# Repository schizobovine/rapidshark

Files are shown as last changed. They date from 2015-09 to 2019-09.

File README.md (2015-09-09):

# RapidShark
Nerf RapidStrike CS-18 mod using an Arduino and LiPo battery upgrade to rain
foamy annoyance upon one's enemies.

The name originally came from my initial idea to use a pair of NSR Shark 40krpm
motors, originally for 12V slot car racing. It quickly became a reference to
Randall Munroe's [XKCD comic about lowering one's standards for success as a
project wears on...]<https://xkcd.com/349/>

# Versions

This project has undergone a number of major and minor redesigns, and my
documentation isn't exactly the best, especially for earlier versions where I
assumed this would be a quick hack involving relatively little electronics
knowledge (oh, to be 3 years younger and less naive...).

* Mark I
*  Completed build
*  Used slightly larger motors: 24mm 12V 12850rpm [PAN14EE12AA1]<http://www.digikey.com/product-detail/en/PAN14EE12AA1/P14346-ND/2417070>
*  Covered cut-outs for above with some horribly done epoxy work
*  4S LiPo battery (14.8V nominal)
*  Flywheels ran directly off battery voltage
*  Rate of fire controlled via diodes (1N5209's?) in series
*  Segmented LED display only showed battery voltage.
*  Extremely noisy, had jamming issues especially at higher ROF
*  Very clumsy controls (giant knob on the side for ROF)
*  Overall, kinda crappy prototype

* Mark II
*  Never finished build
*  Originally going to be 2S LiPo based
*  Proved too noisy for reasonable use

* Mark III
*  Completed build
*  Same [PAN14EE12AA1]<http://www.digikey.com/product-detail/en/PAN14EE12AA1/P14346-ND/2417070> as in Mark I
*  Used heat gun to deform plastic to accomodate motors
*  4S LiPo battery (14.8V nominal)
*  Flywheels again directly off line voltage
*  Rate of fire controlled via stupidly big linear regulator (LM335, then LT1083)
*  Custom PCB from OSHPark for speed controller
*  Actually bothered to paint this one
*  Slightly better slide switch for ROF control
*  Added pushbutton laser "sight" because reasons
*  First attempt at ammo counter using SparkFun Pro Mini 5V to drive a 2 digit segmented display
*  Detected shots at first using IR LED & photodiode, but was too noisy so went to reed switch
*  Button panel for fiddling with/resetting counter
*  Counter was awesome but proved very unreliable in practice
*  Noticable voltage drop-out during flywheel spin-up

* Mark IV
*  Work in progess
*  Skipping paint job to make this one a "sleeper" model
*  Motors unselected but will be 130 Mabuchi form-factor to fit in existing case with little modification
*  Will feature two proper H-bridges, the [Pololu VNH5019 Motor Driver Carrier]<https://www.pololu.com/product/1451>
*  Since the H-bridges will be electronically controlled, switched to subminiature microswitches hooked up to uC (instead of giant 15A microswitches directly flipping current around)
*  [Adafruit Metro Mini]<https://www.adafruit.com/products/2590> as main controller
*  OLED display (either SparkFun Microview or Ye Olde Generic From Ebay)
*  IR interrupter for dart firing detection confirmation, in combination with mechanical position detection for the dart pusher.
*  Whole slew of small custom PCB's to aid in wiring

# License

* AVR C code (basically, everything under the firmware directory) is licensed under the GPLv2.0.
* Everything else is Creative Commons 4.0, Attribution-Share-Sharealike (CC-4.0-BY-SA)

# Acknowledgements

I would not be nearly as far along (or in the ICU from exploding batteries) if
not for the help and previous work & knowledge of
[torukmakto4]<http://torukmakto4.blogspot.co.uk/>; read some of the linked
posts below for a good breakdown of the basic fire control circuit in the
RapidStrike.

I also would like to thank the folks from Blastersmiths UK for their
information shared on [Diaries of a Nerf
Armorurer]<http://nerfarmourer.tumblr.com>, as it both provided inspiration,
guidance, and a lot of helpful pictures for this project.

# References

[The Dart Zone: Wiring and electrical practices]<http://torukmakto4.blogspot.co.uk/2013/04/tech-wiring-and-electrical-practices.html>
[The Dart Zone: Standard Rapidstrike, an Illustrated Guide]<http://torukmakto4.blogspot.co.uk/2013/10/standard-rapidstrike-illustrated-guide.html>
[The Dart Zone: Why compensating for resistance using additional voltage is bad design]<http://torukmakto4.blogspot.co.uk/2014/05/why-compensating-for-resistance-using.html>
[Diaries of a Nerf Armourer: 'Sharked' Rapidstrike CS-18 - Raja and Triakis]<http://nerfarmourer.tumblr.com/post/59029888581/sharked-rapidstrike-cs-18-raja-and-triakis>
[Diaries of a Nerf Armourer: NSR Shark 40 Necrospy]<http://nerfarmourer.tumblr.com/post/69776618533/nsr-shark-40-necrospy>
[Diaries of a Nerf Armourer: Rapidstrike Modification Guide]<http://nerfarmourer.tumblr.com/post/57957334515/rapidstrike-modification-guide-also-commissions>

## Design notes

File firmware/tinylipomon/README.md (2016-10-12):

Tiny Lipo Battery Monitor
=====================

Small ATTiny84 board for monitoring high power lithium polymer batteries
connected in series. Due to differences in manufacturing, the cells in them
will often vary in voltage and capacity, so a close eye must be kept to make
sure none are close to over-charge (>4.2V/cell) or near drained (<3.2V/cell).

This is the firmware for the project, which you should be able to load on an
ATTiny84 of your own using the Ardunio IDE (1.6+) and the attiny board add-on
(available in the board manager).

Probably deserves it's own project, but for now getting stashed here.

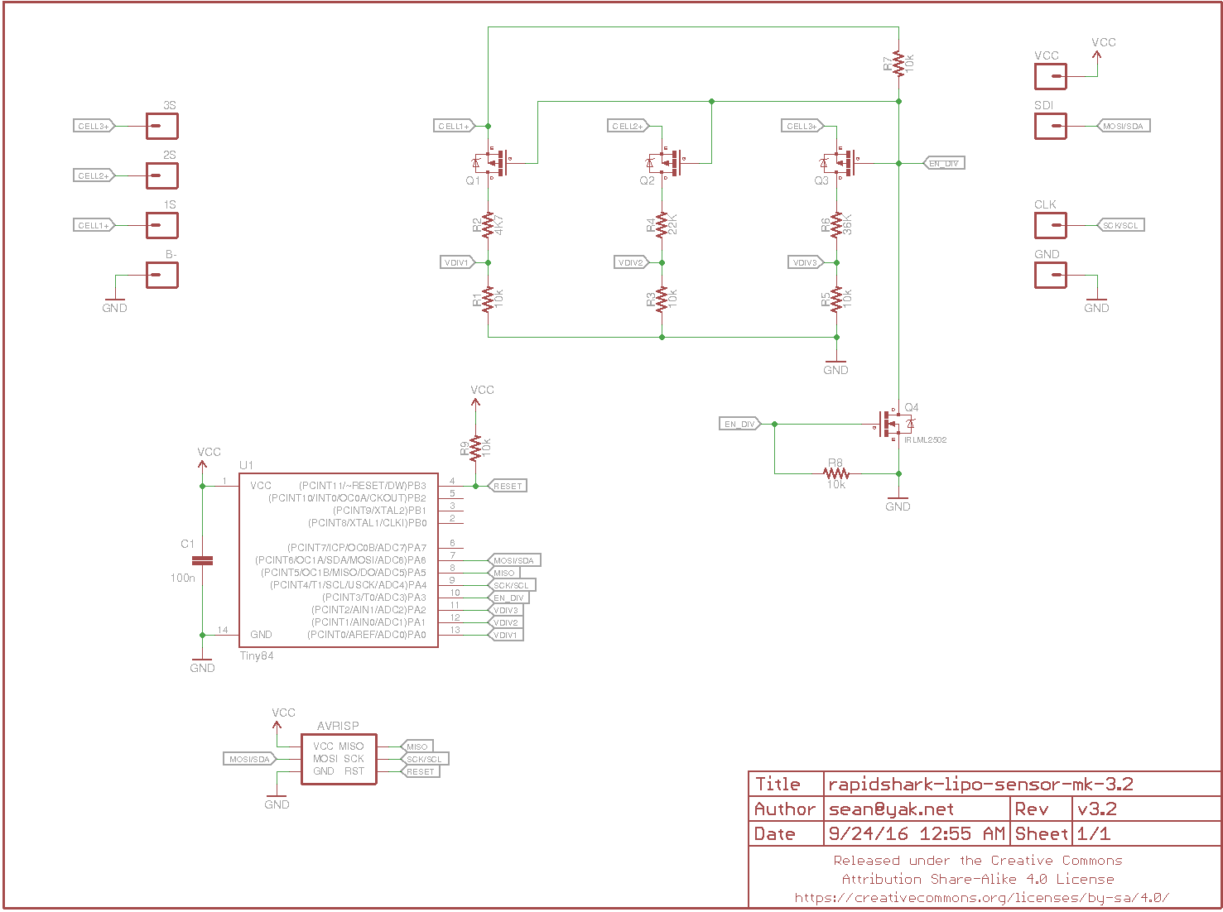
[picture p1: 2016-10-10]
hardware/rapidshark-lipo-sensor-mk-3.2.sch.png

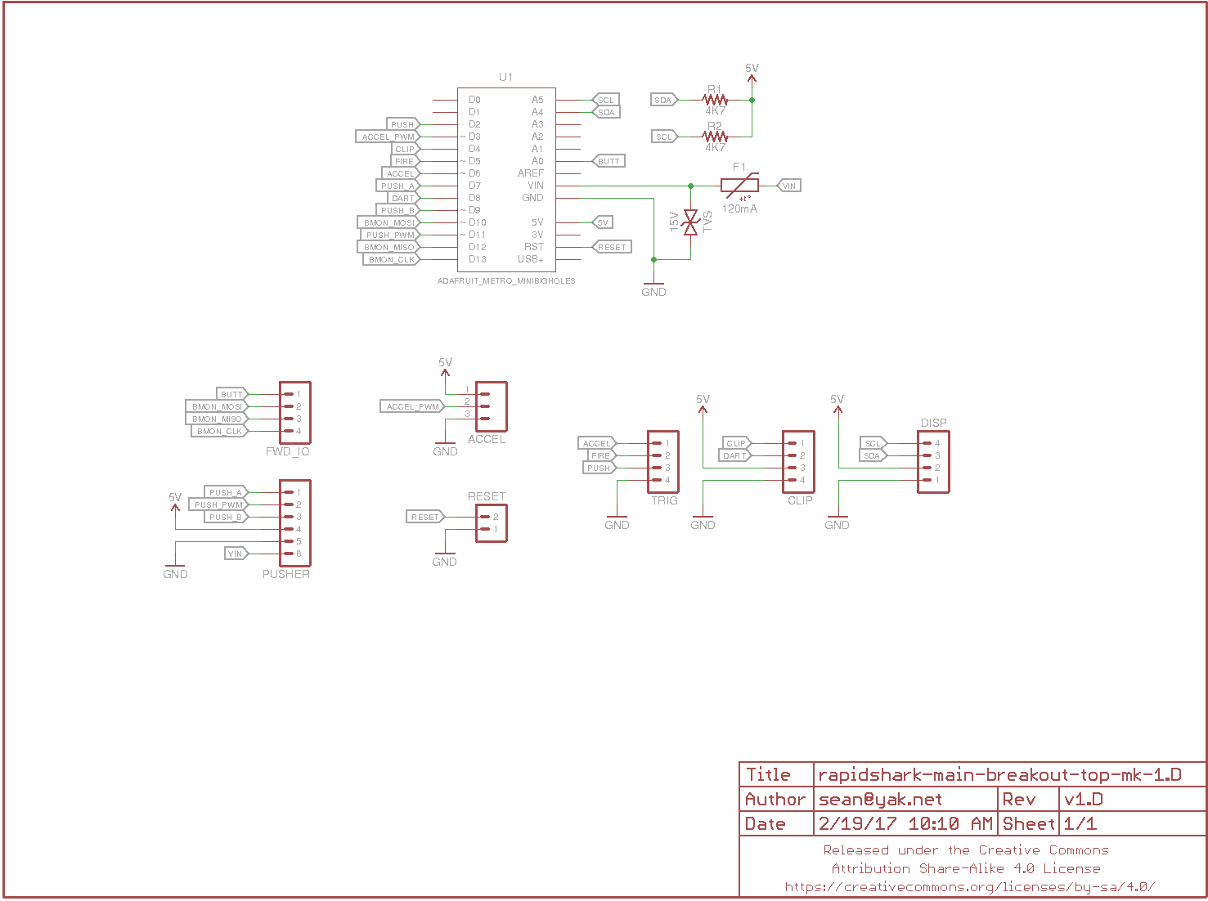
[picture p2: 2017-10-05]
hardware/rapidshark-main-breakout-top-mk-1.D.png

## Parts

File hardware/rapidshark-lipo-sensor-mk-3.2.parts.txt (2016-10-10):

Partlist

Exported from rapidshark-lipo-sensor-mk-3.2.sch at 10/8/16 1:10 AM

EAGLE Version 7.5.0 Copyright (c) 1988-2015 CadSoft

Assembly variant: 

Part     Value                        Device                         Package             Library  Sheet

1S       M01PTH-0.9MM                 M01PTH-0.9MM                   1X01-0.9MM          a_parts  1
2S       M01PTH-0.9MM                 M01PTH-0.9MM                   1X01-0.9MM          a_parts  1
3S       M01PTH-0.9MM                 M01PTH-0.9MM                   1X01-0.9MM          a_parts  1
AVRISP   AVR_SPI_PRG_6SMD_TEST_POINTS AVR_SPI_PRG_6SMD_TEST_POINTS   2X3_SMD_TEST_POINTS A_butts  1
B-       M01PTH-0.9MM                 M01PTH-0.9MM                   1X01-0.9MM          a_parts  1
C1       100n                         CAPACITOR-CERAMICC0603-TIGHTER C0603-TIGHTER       a_parts  1
CLK      M01PTH-0.9MM                 M01PTH-0.9MM                   1X01-0.9MM          a_parts  1
GND      M01PTH-0.9MM                 M01PTH-0.9MM                   1X01-0.9MM          a_parts  1
Q1                                    MOSFET-PCHANNELSOT-23          SOT23               a_parts  1
Q2                                    MOSFET-PCHANNELSOT-23          SOT23               a_parts  1
Q3                                    MOSFET-PCHANNELSOT-23          SOT23               a_parts  1
Q4       IRLML2502                    MOSFET-NCHANNELIRLML2502       SOT23               a_parts  1
R1       10k                          RESISTORR0603-TIGHTER          R0603-TIGHTER       a_parts  1
R2       4K7                          RESISTORR0603-TIGHTER          R0603-TIGHTER       a_parts  1
R3       10k                          RESISTORR0603-TIGHTER          R0603-TIGHTER       a_parts  1
R4       22K                          RESISTORR0603-TIGHTER          R0603-TIGHTER       a_parts  1
R5       10k                          RESISTORR0603-TIGHTER          R0603-TIGHTER       a_parts  1
R6       36K                          RESISTORR0603-TIGHTER          R0603-TIGHTER       a_parts  1
R7       10k                          RESISTORR0603-TIGHTER          R0603-TIGHTER       a_parts  1
R8       10k                          RESISTORR0603-TIGHTER          R0603-TIGHTER       a_parts  1
R9       10k                          RESISTORR0603-TIGHTER          R0603-TIGHTER       a_parts  1
SDI      M01PTH-0.9MM                 M01PTH-0.9MM                   1X01-0.9MM          a_parts  1
U1       Tiny84                       ATTINY84                       SO14                A_butts  1
VCC      M01PTH-0.9MM                 M01PTH-0.9MM                   1X01-0.9MM          a_parts  1

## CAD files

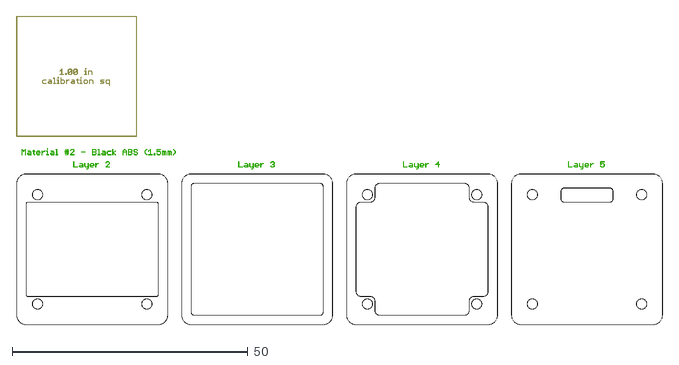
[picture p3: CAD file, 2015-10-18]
hardware/case-for-oled-mk-1.1-abs-black-1.5mm.dxf
137.1 x 65.5

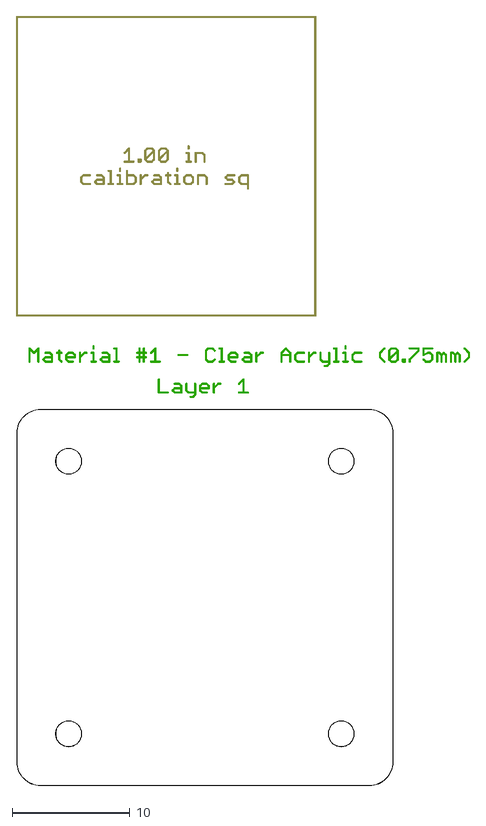
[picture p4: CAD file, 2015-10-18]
hardware/case-for-oled-mk-1.1-pmma-clear-0.75mm.dxf
38.6 x 65.5

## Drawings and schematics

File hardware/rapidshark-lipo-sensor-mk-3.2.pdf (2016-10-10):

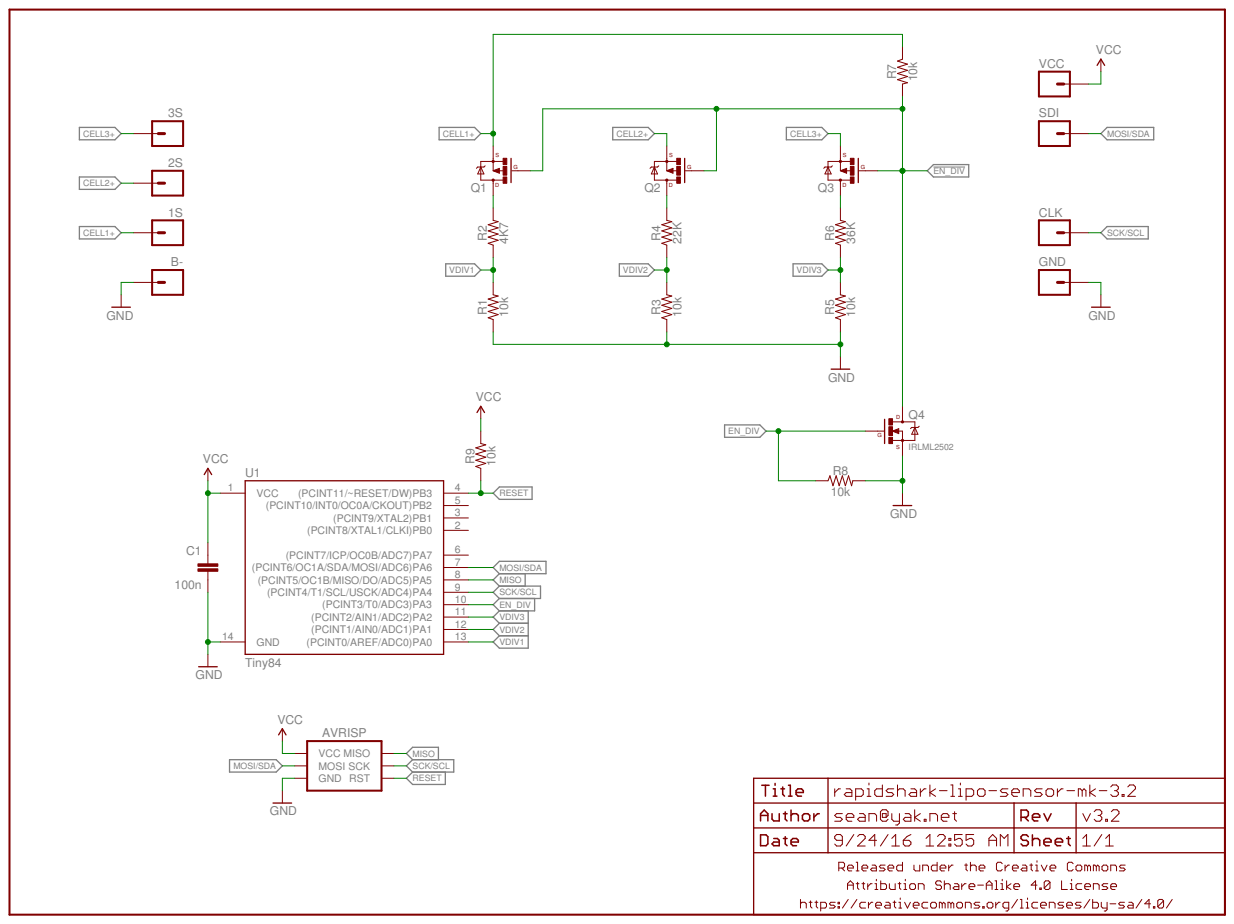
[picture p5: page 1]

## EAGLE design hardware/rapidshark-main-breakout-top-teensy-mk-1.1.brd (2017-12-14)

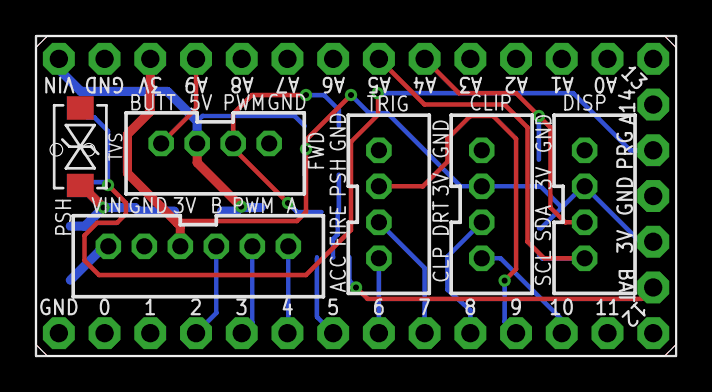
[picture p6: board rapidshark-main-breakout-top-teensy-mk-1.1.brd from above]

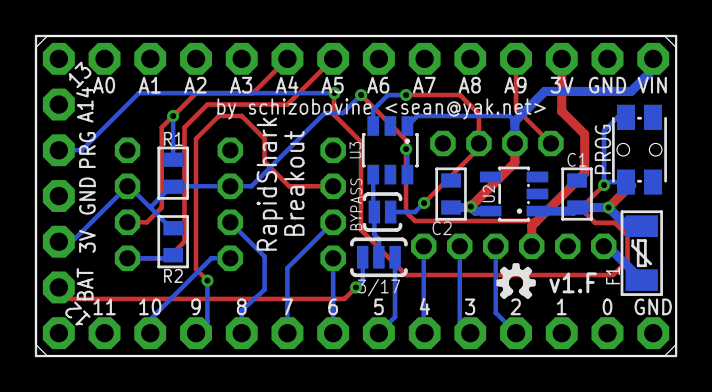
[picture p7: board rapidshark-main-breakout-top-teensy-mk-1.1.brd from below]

Board: 2 copper layers, 35.6 x 17.8 mm, 19 parts (12 on the bottom side), 21 nets.

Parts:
3/17: PAD-JUMPER-3-NO_YES_SILK_FULL_BOX_SMALLER
BYPASS: JUMPER-PAD-2-NOYES_SILK; PAD-JUMPER-2-NO_YES_SILK
C1: 1uF; C0603-TIGHTER
C2: 2.2uF; C0603-TIGHTER
CLIP: M04JST-PTH-VERT; JST-4-PH-VERT-PTH
DISP: M04JST-PTH-VERT; JST-4-PH-VERT-PTH
F1: 120mA; PTC-1206
FRAME1: FRAME-LETTERNO_PACKAGE; DUMMY
FWD: M04JST-PTH-VERT; JST-4-PH-VERT-PTH
PROG: SPST-NO-TACTCK-PTS840-GK; TACTILE-SMD-CK-PTS840-GK
PSH: M06JST-PH-PTH-VERT; JST-6-PH-VERT-PTH
R1, R2: 4K7; R0603-TIGHTER
TRIG: M04JST-PTH-VERT; JST-4-PH-VERT-PTH
TVS: 15V; SMA-DIODE-TVS-BIDIR
U1: TEENSY-3.1-OUTERPTH; TEENSY-3.1_OUTERONLY
U2: MIC5235; SOT23-5
U3: SN74LVC1T45SOT23-6; SOT23-6
U$3: OSHWLOGO_TINY_SILKONLY

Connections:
3.3V: CLIP.2, DISP.2, PSH.4, R1.2, R2.2, U1.3.3V, U1.3V, U3.6
5: 3/17.1, U1.5
5V: C2.1, FWD.3, U1.VIN, U2.5, U3.1
17: 3/17.3, U1.VBAT
ACCEL: TRIG.4, U1.6
ACCEL_PWM: 3/17.2, BYPASS.1, U3.4
ACCEL_PWM_5V: BYPASS.2, FWD.2, U3.3
BUTT: FWD.4, U1.23
CLIP: CLIP.4, U1.10
DART: CLIP.3, U1.8
FIRE: TRIG.3, U1.7
GND: C1.2, C2.2, CLIP.1, DISP.1, FWD.1, PROG.3, PROG.4, PSH.5, TRIG.1, TVS.1, U1.AGND, U1.GND, U1.GND1, U2.2, U3.2, U3.5
PROG: PROG.1, PROG.2, U1.PROG
PUSH: TRIG.2, U1.9
PUSH_A: PSH.1, U1.4
PUSH_B: PSH.3, U1.2
PUSH_PWM: PSH.2, U1.3
SCL: DISP.4, R2.1, U1.19
SDA: DISP.3, R1.1, U1.18
VIN: C1.1, F1.2, TVS.2, U2.1, U2.3
VRAW: F1.1, PSH.6

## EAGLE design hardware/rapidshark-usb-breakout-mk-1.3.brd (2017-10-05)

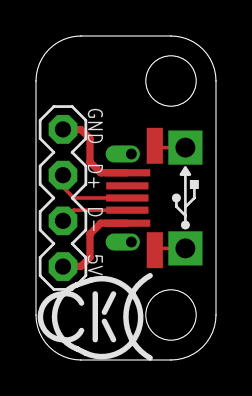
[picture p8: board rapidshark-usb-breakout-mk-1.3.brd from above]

Board: 2 copper layers, 10.0 x 18.0 mm, 4 parts (1 on the bottom side), 4 nets.

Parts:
FRAME1: FRAME-LETTERNO_PACKAGE; DUMMY
JP1: M04PTH-CENTERED; 1X04-PTH-VERT-CENTER
U$1: COW_SMALL_NOTEXT
USB1: USB-AB-SHIELDFCI-10103594-USB-MICRO-B-EVENLESS; FCI-10103594-USB-MICRO-B-EVENLESS

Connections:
5V: JP1.4, USB1.1
DATA_M: JP1.3, USB1.2
DATA_P: JP1.2, USB1.3
GND: JP1.1, USB1.5, USB1.SHIELD@1, USB1.SHIELD@2, USB1.SHIELD@3, USB1.SHIELD@4, USB1.SHIELD@5, USB1.SHIELD@6

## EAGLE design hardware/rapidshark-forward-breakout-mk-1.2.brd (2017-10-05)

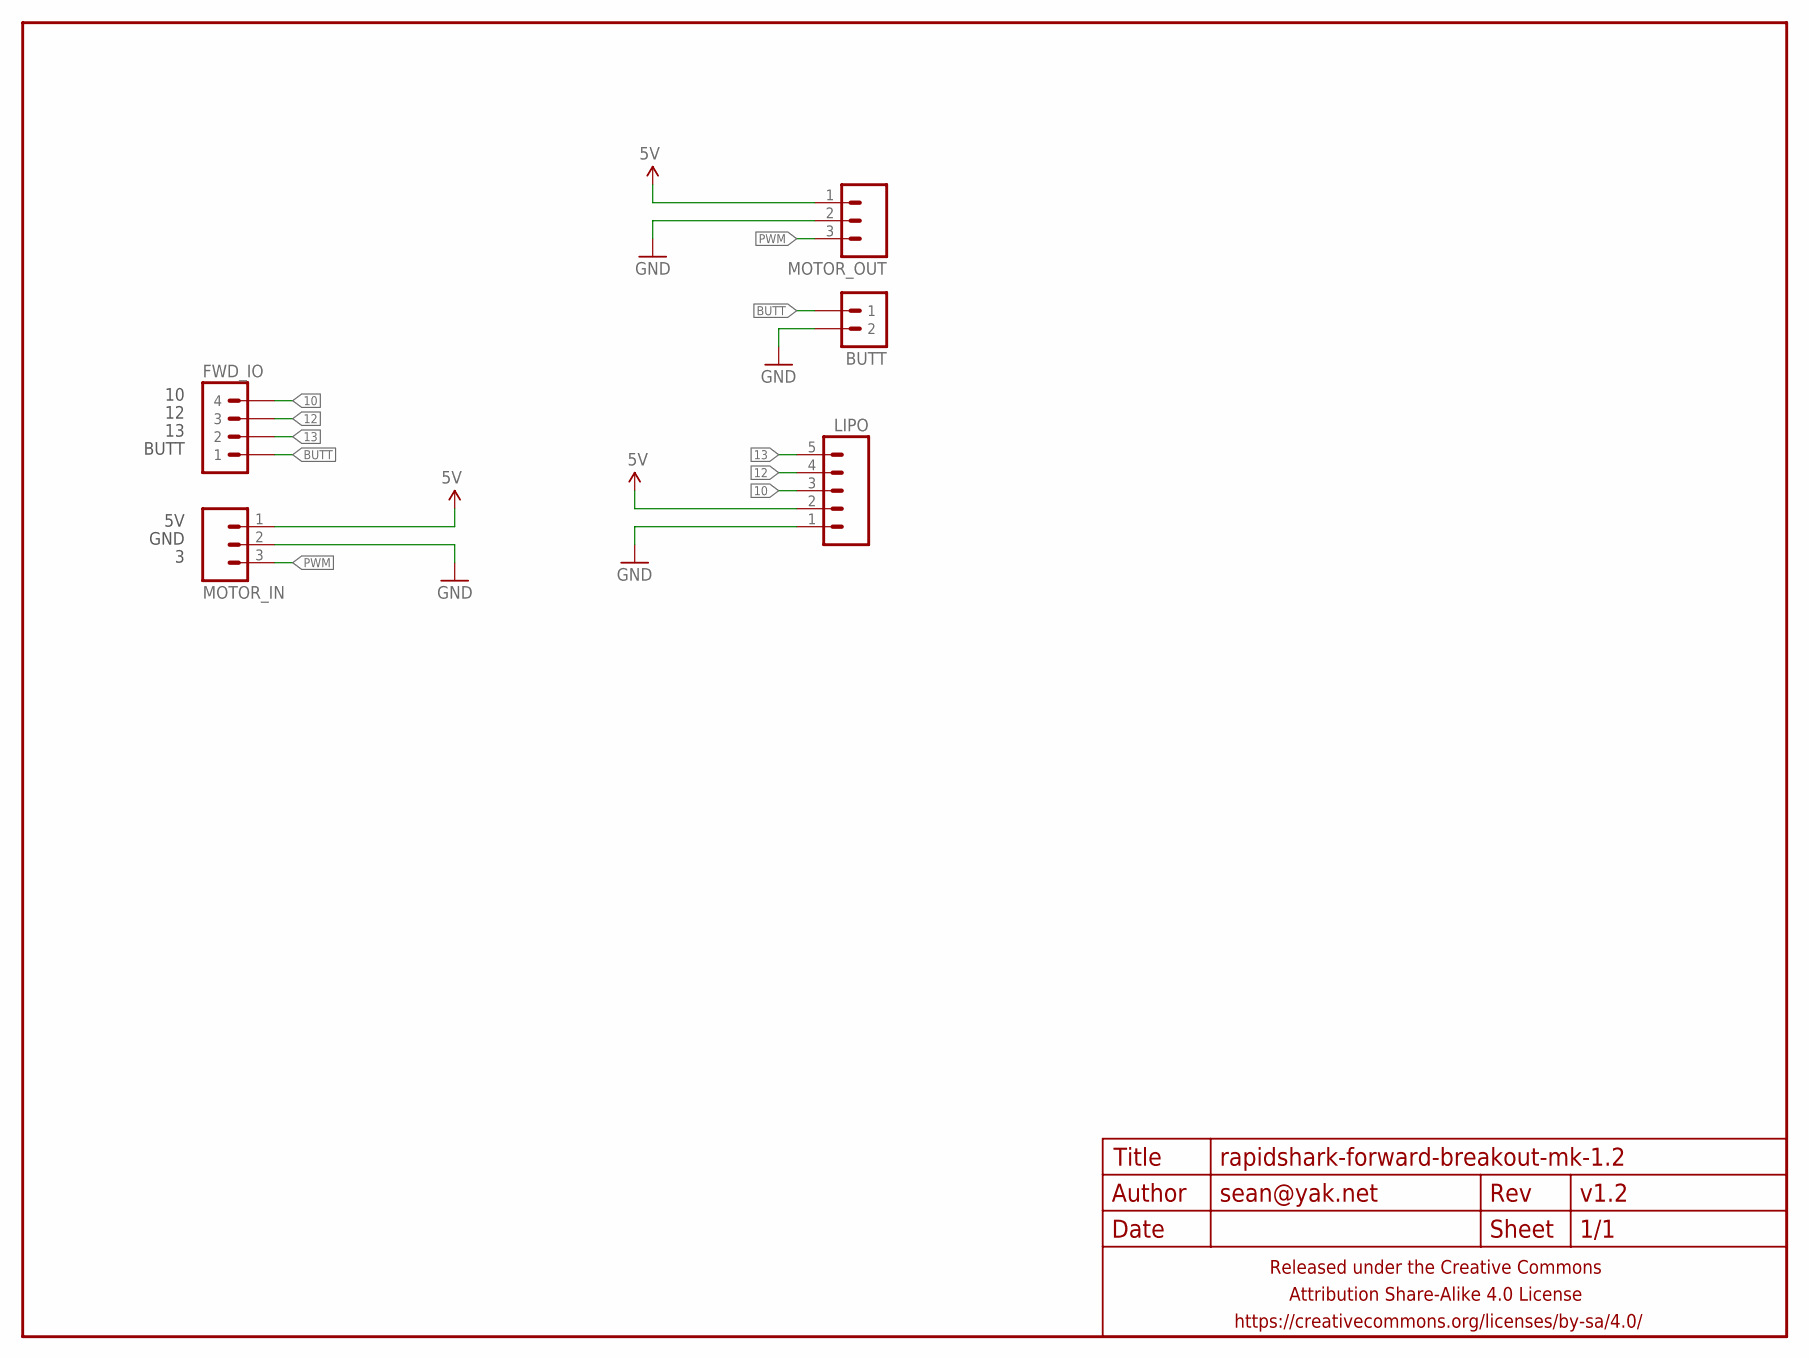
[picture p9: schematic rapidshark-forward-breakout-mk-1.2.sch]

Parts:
BUTT: M02JST-PTH-VERT; JST-2-PH-VERT-PTH
FRAME1: FRAME-LETTERNO_PACKAGE; DUMMY
FWD_IO: M04JST-PTH-VERT; JST-4-PH-VERT-PTH
LIPO: M05JST-PH-VERT-PTH; JST-5-PH-VERT-PTH
MOTOR_IN: M03JST-PTH-VERT; JST-3-PH-VERT-PTH
MOTOR_OUT: M03JST-PTH-VERT; JST-3-PH-VERT-PTH

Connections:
5V: LIPO.2, MOTOR_IN.1, MOTOR_OUT.1
10: FWD_IO.4, LIPO.3
12: FWD_IO.3, LIPO.4
13: FWD_IO.2, LIPO.5
BUTT: BUTT.1, FWD_IO.1
GND: BUTT.2, LIPO.1, MOTOR_IN.2, MOTOR_OUT.2
PWM: MOTOR_IN.3, MOTOR_OUT.3

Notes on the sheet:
GND
BUTT

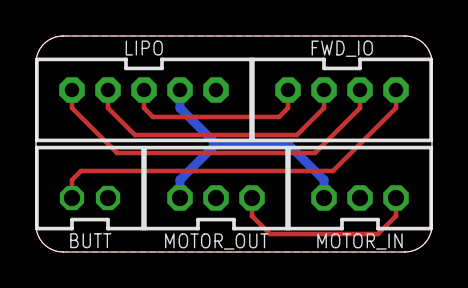
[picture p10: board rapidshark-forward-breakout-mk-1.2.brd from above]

Board: 2 copper layers, 22.0 x 12.0 mm, 6 parts (1 on the bottom side), 7 nets.

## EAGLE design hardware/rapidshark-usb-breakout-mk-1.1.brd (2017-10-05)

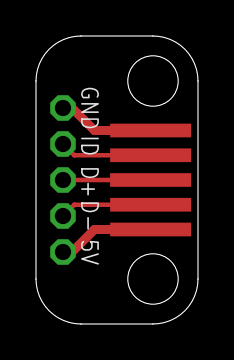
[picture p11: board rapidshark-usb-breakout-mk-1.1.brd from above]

Board: 2 copper layers, 9.0 x 16.0 mm, 3 parts (1 on the bottom side), 5 nets.

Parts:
FRAME1: FRAME-LETTERNO_PACKAGE; DUMMY
JP1: M052MMPTH; 1X05-0.9X2MM-PTH
U1: ADAFRUIT_USB_PANEL_MOUNT

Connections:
5V: JP1.5, U1.5
DATA_M: JP1.4, U1.4
DATA_P: JP1.3, U1.3
GND: JP1.1, U1.1
ID: JP1.2, U1.2

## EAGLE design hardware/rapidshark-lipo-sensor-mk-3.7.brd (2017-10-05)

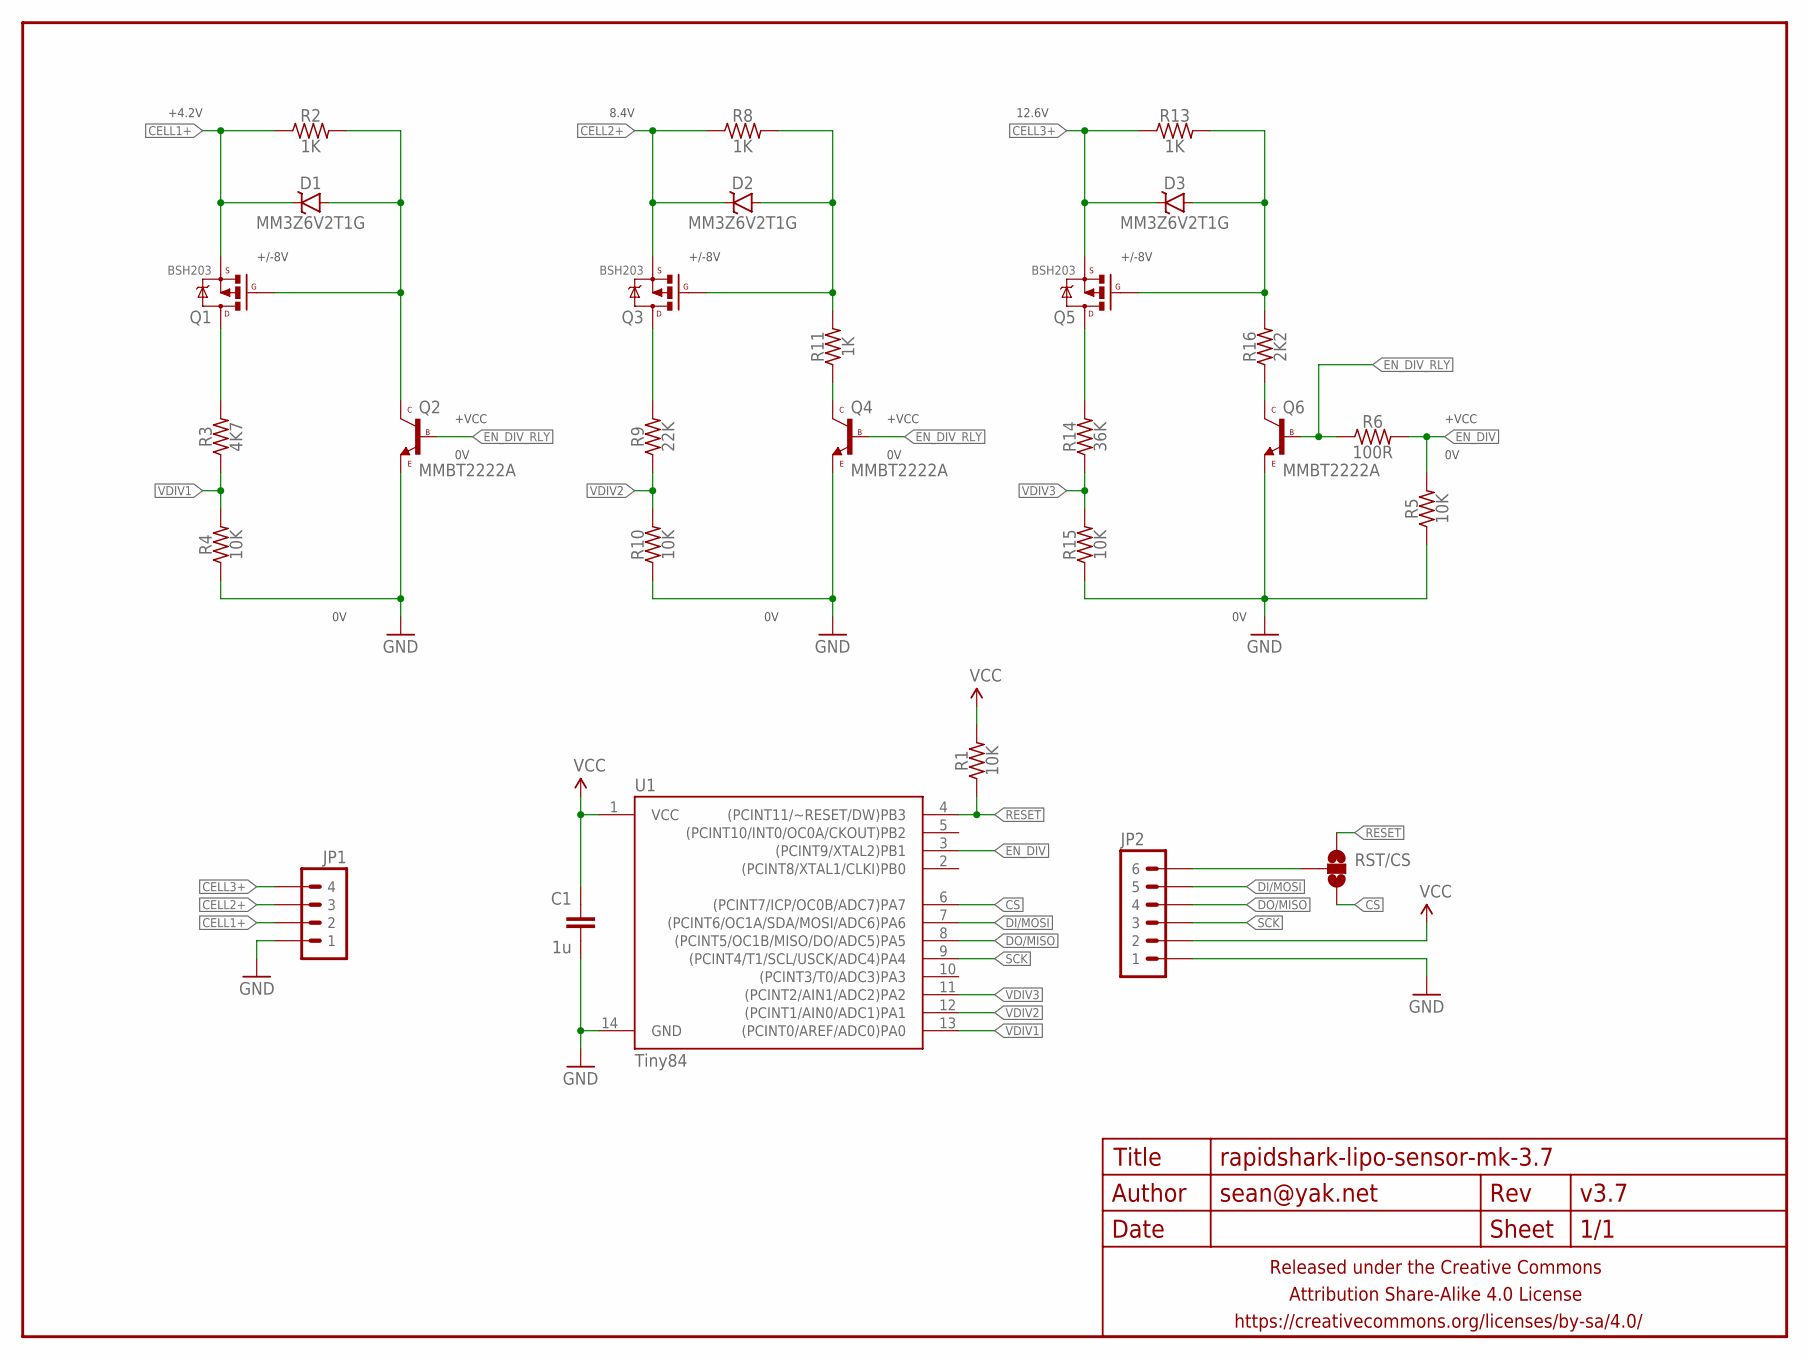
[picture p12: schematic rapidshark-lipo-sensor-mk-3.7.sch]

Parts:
C1: 1u; C0603-TIGHTER
D1, D2, D3: MM3Z6V2T1G; SOD323-ZENNER
FRAME1: FRAME-LETTERNO_PACKAGE; DUMMY
JP1: M04JST_XH_RA; JST-4-XH-RA-PTH
JP2: M06PTH_CENTERED; 1X06_CENTERED
Q1, Q3, Q5: BSH203; SOT23
Q2, Q4, Q6: MMBT2222A; SOT23
R1, R4, R5, R10, R15: 10K; R0603-TIGHTER
R2, R8, R11, R13: 1K; R0603-TIGHTER
R3: 4K7; R0603-TIGHTER
R6: 100R; R0603-TIGHTER
R9: 22K; R0603-TIGHTER
R14: 36K; R0603-TIGHTER
R16: 2K2; R0603-TIGHTER
RST/CS: JUMPER-PAD-3-NOFULL_BOX_SILK; PAD-JUMPER-3-NO_YES_SILK_FULL_BOX
U1: Tiny84; SO14

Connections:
CELL1+: D1.C, JP1.2, Q1.2 (S), R2.1
CELL2+: D2.C, JP1.3, Q3.2 (S), R8.1
CELL3+: D3.C, JP1.4, Q5.2 (S), R13.1
CS: RST/CS.3, U1.6 ((PCINT7/ICP/OC0B/ADC7)PA7)
DI/MOSI: JP2.5, U1.7 ((PCINT6/OC1A/SDA/MOSI/ADC6)PA6)
DO/MISO: JP2.4, U1.8 ((PCINT5/OC1B/MISO/DO/ADC5)PA5)
EN_DIV: R5.2, R6.2, U1.3 ((PCINT9/XTAL2)PB1)
EN_DIV_RLY: Q2.1 (B), Q4.1 (B), Q6.1 (B), R6.1
GND: C1.2, JP1.1, JP2.1, Q2.2 (E), Q4.2 (E), Q6.2 (E), R4.1, R5.1, R10.1, R15.1, U1.14 (GND)
unnamed: Q4.3 (C), R11.1
unnamed: Q3.3 (D), R9.2
unnamed: Q5.3 (D), R14.2
unnamed: D2.A, Q3.1 (G), R8.2, R11.2
unnamed: Q1.3 (D), R3.2
unnamed: D3.A, Q5.1 (G), R13.2, R16.2
unnamed: Q6.3 (C), R16.1
unnamed: D1.A, Q1.1 (G), Q2.3 (C), R2.2
RESET: R1.1, RST/CS.1, U1.4 ((PCINT11/~RESET/DW)PB3)
RST/CS: JP2.6, RST/CS.2
SCK: JP2.3, U1.9 ((PCINT4/T1/SCL/USCK/ADC4)PA4)
VCC: C1.1, JP2.2, R1.2, U1.1 (VCC)
VDIV1: R3.1, R4.2, U1.13 ((PCINT0/AREF/ADC0)PA0)
VDIV2: R9.1, R10.2, U1.12 ((PCINT1/AIN0/ADC1)PA1)
VDIV3: R14.1, R15.2, U1.11 ((PCINT2/AIN1/ADC2)PA2)

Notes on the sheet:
+4.2V
8.4V
12.6V
+VCC
+/-8V

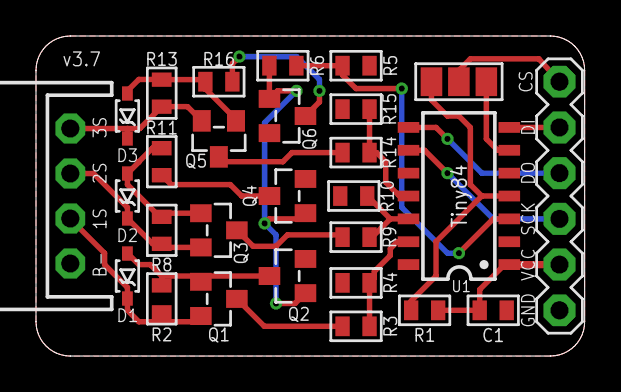
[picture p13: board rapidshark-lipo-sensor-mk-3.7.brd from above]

Board: 2 copper layers, 30.5 x 17.8 mm, 29 parts (0 on the bottom side), 24 nets.

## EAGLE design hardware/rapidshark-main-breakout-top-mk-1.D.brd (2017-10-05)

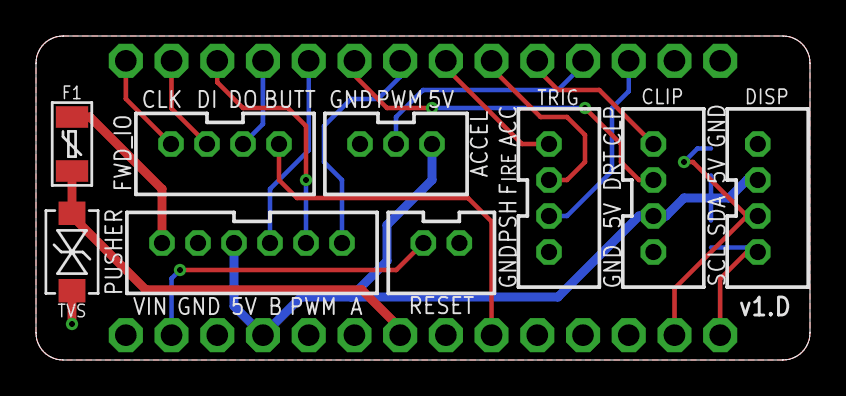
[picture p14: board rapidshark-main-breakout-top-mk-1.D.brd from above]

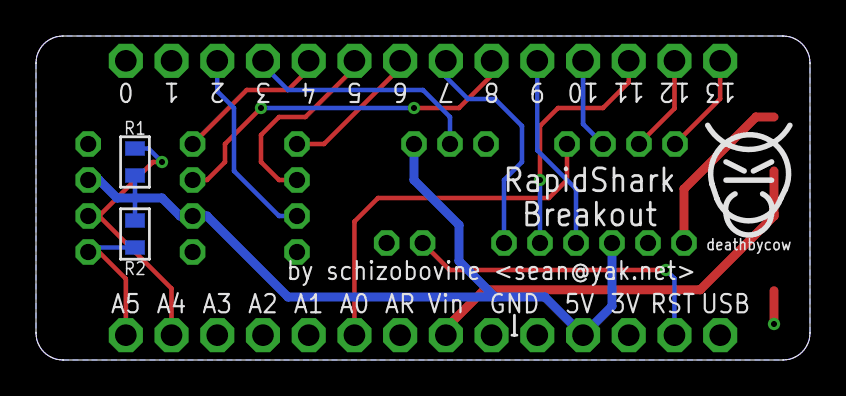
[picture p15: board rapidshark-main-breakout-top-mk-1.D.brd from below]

Board: 2 copper layers, 43.0 x 18.0 mm, 14 parts (4 on the bottom side), 20 nets.

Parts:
ACCEL: M03JST-PTH-VERT-CENTERED; JST-3-PH-VERT-PTH-CENTERED
CLIP: M04JST-PTH-VERT; JST-4-PH-VERT-PTH
DISP: M04JST-PTH-VERT; JST-4-PH-VERT-PTH
F1: 120mA; PTC-1206
FRAME1: FRAME-LETTERNO_PACKAGE; DUMMY
FWD_IO: M04JST-PTH-VERT; JST-4-PH-VERT-PTH
PUSHER: M06JST-PH-PTH-VERT; JST-6-PH-VERT-PTH
R1, R2: 4K7; R0603-TIGHTER
RESET: M02JST-PTH-VERT; JST-2-PH-VERT-PTH
TRIG: M04JST-PTH-VERT; JST-4-PH-VERT-PTH
TVS: 15V; SMA-DIODE-TVS-BIDIR
U1: ADAFRUIT_METRO_MINIBIGHOLES; ADAFRUIT_METRO_MINI_BIGHOLES
U$2: COW_SMALL

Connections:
5V: ACCEL.1, CLIP.3, DISP.2, PUSHER.4, R1.2, R2.2, U1.18
ACCEL: TRIG.1, U1.7
ACCEL_PWM: ACCEL.2, U1.4
BMON_CLK: FWD_IO.4, U1.14
BMON_MISO: FWD_IO.3, U1.13
BMON_MOSI: FWD_IO.2, U1.11
BUTT: FWD_IO.1, U1.23
CLIP: CLIP.1, U1.5
DART: CLIP.2, U1.9
FIRE: TRIG.2, U1.6
GND: ACCEL.3, CLIP.4, DISP.1, PUSHER.5, RESET.1, TRIG.4, TVS.1, U1.19, U1.20
unnamed: F1.1, TVS.2, U1.21
PUSH: TRIG.3, U1.3
PUSH_A: PUSHER.1, U1.8
PUSH_B: PUSHER.3, U1.10
PUSH_PWM: PUSHER.2, U1.12
RESET: RESET.2, U1.16
SCL: DISP.4, R2.1, U1.28
SDA: DISP.3, R1.1, U1.27
VIN: F1.2, PUSHER.6

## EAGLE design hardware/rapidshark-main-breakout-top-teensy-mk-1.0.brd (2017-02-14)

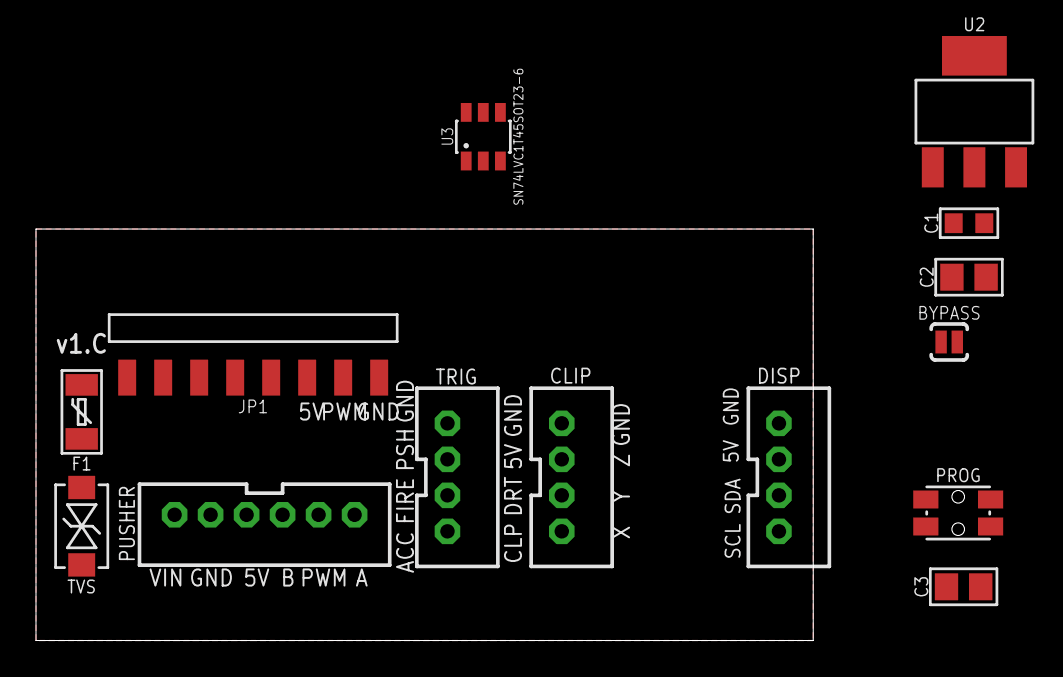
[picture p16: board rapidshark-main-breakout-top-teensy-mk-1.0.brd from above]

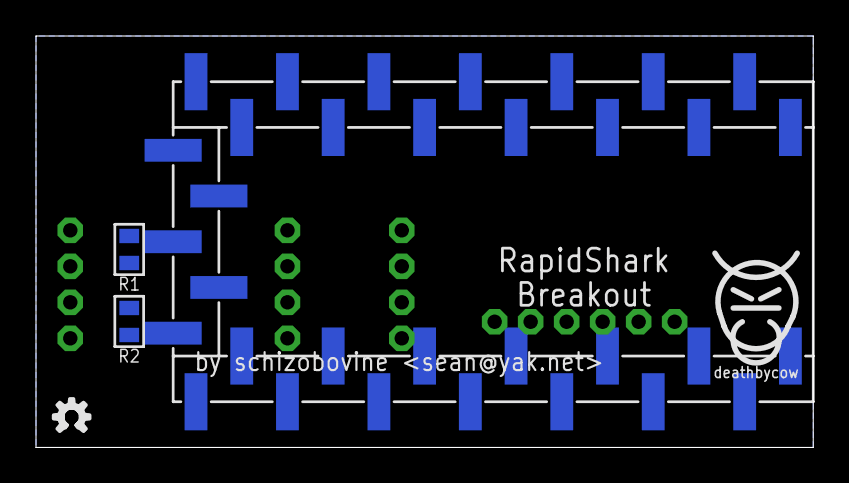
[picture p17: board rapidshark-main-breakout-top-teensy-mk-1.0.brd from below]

Board: 2 copper layers, 43.2 x 22.9 mm, 20 parts (5 on the bottom side), 19 nets, no tracks yet.

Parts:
BYPASS: JUMPER-PAD-2-NOYES_SILK; PAD-JUMPER-2-NO_YES_SILK
C1: 1uF; C0603
C2, C3: 10uF; C0805
CLIP: M04JST-PTH-VERT; JST-4-PH-VERT-PTH
DISP: M04JST-PTH-VERT; JST-4-PH-VERT-PTH
F1: 120mA; PTC-1206
FRAME1: FRAME-LETTERNO_PACKAGE; DUMMY
JP1: M08SMD-RA-MALE-2MM; 1X08_SMD_RA_MALE_2MM
PROG: SPST-NO-TACTCK-PTS840-GK; TACTILE-SMD-CK-PTS840-GK
PUSHER: M06JST-PH-PTH-VERT; JST-6-PH-VERT-PTH
R1, R2: 4K7; R0603-TIGHTER
TRIG: M04JST-PTH-VERT; JST-4-PH-VERT-PTH
TVS: 15V; SMA-DIODE-TVS-BIDIR
U1: TEENSY-3.1-OUTERSMT; TEENSY-3.1_SMT_BOTTOM_OUTERONLY
U2: LD1117-5V; SOT223
U3: SN74LVC1T45SOT23-6; SOT23-6
U$2: COW_SMALL
U$3: OSHWLOGO_TINY_SILKONLY

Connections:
3.3V: C3.1, CLIP.2, DISP.2, JP1.5, PUSHER.4, R1.2, R2.2, U1.3V3, U1.3V3@1, U3.6
5V: C2.1, JP1.6, U1.VIN, U2.2, U2.4, U3.1
ACCEL: TRIG.4, U1.6
ACCEL_PWM: BYPASS.1, U1.9, U3.4
ACCEL_PWM_5V: BYPASS.2, JP1.7, U3.3
BMON_CLK: JP1.4, U1.13
BMON_DI: JP1.2, U1.12
BMON_DO: JP1.3, U1.11
BUTT: JP1.1, U1.14/A0
CLIP: CLIP.4, U1.4
DART: CLIP.3, U1.2
FIRE: TRIG.3, U1.5
GND: C1.2, C2.2, C3.2, CLIP.1, DISP.1, JP1.8, PROG.3, PROG.4, PUSHER.5, TRIG.1, TVS.1, U1.AGND, U1.GND, U1.GND@1, U2.1, U3.2, U3.5
unnamed: C1.1, F1.2, TVS.2, U2.3
PROG: PROG.1, PROG.2, U1.PROG
PUSH: TRIG.2, U1.3
SCL: DISP.4, R2.1, U1.19/A5
SDA: DISP.3, R1.1, U1.18/A4
VIN: F1.1, PUSHER.6

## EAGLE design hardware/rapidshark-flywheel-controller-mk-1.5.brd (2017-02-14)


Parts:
C1: 1uF; C0603-TIGHTER
C3: CAPACITOR-CERAMICC0603-TIGHTER; C0603-TIGHTER
FRAME1: FRAME-LETTERNO_PACKAGE; DUMMY
I2C: M04-I2CJST-4-PH-RA-CENTERED; 1X04-JST-PH-RA-PTH-I2C-CENTERED
IC1: ATTINY84; SO14
JP1: M081X08; 1X08
R1: 10k; RESISTOR-AXIAL-PTH-5.08MM

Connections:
5V: C1.1, I2C.2 (VCC), IC1.1 (VCC), JP1.2, R1.P$2 (2)
CS: IC1.6 ((PCINT7/ICP/OC0B/ADC7)PA7), JP1.5
ENABLE_A: IC1.3 ((PCINT9/XTAL2)PB1), JP1.7
ENABLE_B: IC1.12 ((PCINT1/AIN0/ADC1)PA1), JP1.4
GND: C1.2, I2C.1 (GND), IC1.14 (GND), JP1.1
IN_A: IC1.2 ((PCINT8/XTAL1/CLKI)PB0), JP1.8
IN_B: IC1.13 ((PCINT0/AREF/ADC0)PA0), JP1.3
MISO: IC1.8 ((PCINT5/OC1B/MISO/DO/ADC5)PA5)
MOSI/SDA: I2C.3 (SDA), IC1.7 ((PCINT6/OC1A/SDA/MOSI/ADC6)PA6)
PWM: IC1.5 ((PCINT10/INT0/OC0A/CKOUT)PB2), JP1.6
RESET: IC1.4 ((PCINT11/~RESET/DW)PB3), R1.P$1 (1)
SCK/SCL: I2C.4 (SCL), IC1.9 ((PCINT4/T1/SCL/USCK/ADC4)PA4)

Board: 2 copper layers, 7 parts (1 on the bottom side), 11 nets, no tracks yet.

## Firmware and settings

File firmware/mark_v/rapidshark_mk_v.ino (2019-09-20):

/*
 * rapidshark_mark_v.ino
 *
 * Arduino microcontroller code to do All The Things to make darts fly.
 *
 * Author: Sean "schizobovine" Caulfield <sean@yak.net>
 * License: GPLv2 (firmware) / CC4.0-BY-SA (documentation, hardware)
 *
 */

#include <Arduino.h>
#include <Adafruit_GFX.h>
#include <Adafruit_SSD1306.h>
#include <Bounce2.h>
#include <SPI.h>
#include <Wire.h>
//#include <EnableInterrupt.h>
#include <FreqMeasure.h>

////////////////////////////////////////////////////////////////////////
// PIN CONFIGURATION & COMPILE TIME SETTINGS
////////////////////////////////////////////////////////////////////////

#define PIN_SW_PUSH     2
#define PIN_ACCL_PWM    3
#define PIN_SW_CLIP     4
#define PIN_SW_ACCL     5
#define PIN_SW_FIRE     6
#define PIN_PUSH_A      7
#define PIN_TACHOMETER  8
#define PIN_PUSH_B      9
#define PIN_PUSH_PWM    11
#define PIN_SW_BUTT     13
#define PIN_DISP_RST    -1

#define DEBOUNCE_PUSH       (10)
#define DEBOUNCE_CLIP       (10)
#define DEBOUNCE_FIRE       (50)
#define DEBOUNCE_ACCL       (50)
#define DEBOUNCE_BUTT       (50)

#define DISP_ADDR       0x3C
#define DISP_MODE       SSD1306_SWITCHCAPVCC
#define DISP_TEXT_SMALL 1
#define DISP_TEXT_LARGE 2
#define DISP_COLOR      WHITE

//
// Helper macros for readability
//
#define IS_PUSH_EXTENDED  (switchPush.read()==HIGH)
//#define IS_PUSH_RETRACTED (switchPush.read()==LOW)
//#define IS_ACCL_OPEN      (switchAccl.read()==HIGH)
#define IS_ACCL_CLOSED    (switchAccl.read()==LOW)
#define IS_FIRE_OPEN      (switchFire.read()==HIGH)
#define IS_FIRE_CLOSED    (switchFire.read()==LOW)
#define IS_CLIP_INSERTED  (switchClip.read()==HIGH)
#define IS_FULL_AUTO      (fireMode == FIREMODE_FULLAUTO)
#define KEEP_FIRING       (IS_FULL_AUTO || burstCount > 0)

#define FIREMODE_SINGLE   0
#define FIREMODE_BURST    1
#define FIREMODE_FULLAUTO 2

#define BURST_MODE_ROUNDS 3

// Pusher motor PWM settings
#define PUSH_PWM_GO    96
#define PUSH_PWM_BRAKE 255

// Accel motor PWM setting(s)
#define ACCL_PWM_GO    128
#define ACCL_PWM_BRAKE 0

////////////////////////////////////////////////////////////////////////
// GLOBAL VARIABLES
////////////////////////////////////////////////////////////////////////

// Display controller
Adafruit_SSD1306 display(PIN_DISP_RST);

// Button/switch debouncers
Bounce switchPush;
Bounce switchClip;
Bounce switchFire;
Bounce switchAccl;
Bounce switchButt;

// Ammo counter
uint8_t dartCount = 37;

// Burst shot counter
uint8_t burstCount = BURST_MODE_ROUNDS;

// Current fire mode
uint8_t fireMode = FIREMODE_SINGLE;

////////////////////////////////////////////////////////////////////////
// MOTOR STATE MACHINE
////////////////////////////////////////////////////////////////////////

// Set pusher motor state based on current conditions (are we firing? are there
// burst rounds left to fire? etc.).
void setPushState() {

  // If pusher switch is open, this means it's extended outward and needs to be
  // retracted no matter what; or if we have rounds left to fire for the
  // current mode.
  if (IS_PUSH_EXTENDED) {
    pusher_go();
  }

  // If the fire trigger is open, user has let go of it, and so yank brake to
  // stop pusher and thus stop firing.
  else if (IS_FIRE_OPEN) {
    pusher_brake();

  // Trigger held down, so activate depending on fire control mode and
  // potentially burst counter: keep plugging away for full auto mode; for
  // burst/semi, only activate if we have shots remaining
  } else if (KEEP_FIRING) {
    pusher_go();
  }

  // Otherwise brake motor
  else {
    pusher_brake();
  }
  
}

// Set flywheel motor state based on current conditions
void setAcclState() {

  // If the acceleration trigger is being pushed OR if the fire trigger is
  // being pushed & we're supposed to be firing, run motors
  if (IS_ACCL_CLOSED || ((IS_FIRE_CLOSED) && (KEEP_FIRING))) {
    analogWrite(PIN_ACCL_PWM, ACCL_PWM_GO);
    FreqMeasure.begin();
  }

  // Otherwise, brake motor & reset tach
  else {
    analogWrite(PIN_ACCL_PWM, ACCL_PWM_BRAKE);
    FreqMeasure.end();
  }

}

////////////////////////////////////////////////////////////////////////
// INTERRUPT HANDLERS
////////////////////////////////////////////////////////////////////////

void irq_sw_push() {
  if (switchPush.update()) {
    // Update motor state
  }
}

void irq_sw_fire() {
  if (switchFire.update()) {
    // Update motor state
  }
}

void irq_sw_accl() {
  if (switchAccl.update()) {
    // Update motor state
  }
}

void irq_sw_clip() {
  if (switchClip.update()) {
    // Update ammo counter state
  }
}

void irq_sw_butt() {
  if (switchButt.update()) {
    // Update fire mode
  }
}

////////////////////////////////////////////////////////////////////////
// HELPER FUNCTIONS
////////////////////////////////////////////////////////////////////////

// Engage pusher motor to start shoving out darts!
void pusher_go() {
  digitalWrite(PIN_PUSH_A, HIGH);
  digitalWrite(PIN_PUSH_B, LOW);
  analogWrite(PIN_PUSH_PWM, PUSH_PWM_GO);
}

// Actively brake pusher motor to keep the pusher from being left sticking out.
void pusher_brake() {
  digitalWrite(PIN_PUSH_A, LOW);
  digitalWrite(PIN_PUSH_B, LOW);
  analogWrite(PIN_PUSH_PWM, PUSH_PWM_BRAKE);
}

////////////////////////////////////////////////////////////////////////
// SETUP
////////////////////////////////////////////////////////////////////////

void setup() {

  // Initialize debouncers & set pin mode
  switchPush.attach(PIN_SW_PUSH, INPUT_PULLUP, DEBOUNCE_PUSH);
  switchClip.attach(PIN_SW_CLIP, INPUT_PULLUP, DEBOUNCE_CLIP);
  switchFire.attach(PIN_SW_FIRE, INPUT_PULLUP, DEBOUNCE_FIRE);
  switchAccl.attach(PIN_SW_ACCL, INPUT_PULLUP, DEBOUNCE_ACCL);
  switchAccl.attach(PIN_SW_BUTT, INPUT_PULLUP, DEBOUNCE_BUTT);

  // Register interrupt handlers which invoke debouncers
  //attachInterrupt(PIN_SW_PUSH, irq_sw_push, CHANGE);
  //attachInterrupt(PIN_SW_CLIP, irq_sw_clip, CHANGE);
  //attachInterrupt(PIN_SW_FIRE, irq_sw_fire, CHANGE);
  //attachInterrupt(PIN_SW_ACCL, irq_sw_accl, CHANGE);
  //attachInterrupt(PIN_SW_BUTT, irq_sw_butt, FALLING);
  
  // Setup i2c & display
  Wire.begin();
  display.begin(DISP_MODE, DISP_ADDR);
  display.clearDisplay();
  display.setTextSize(DISP_TEXT_LARGE);
  display.setTextWrap(false);
  display.println();
  display.print("RapidShark");
  display.print("  Mark IV");
  display.dim(false);
  display.display();

}

////////////////////////////////////////////////////////////////////////
// MAIN LOOP
////////////////////////////////////////////////////////////////////////

void loop() {
}

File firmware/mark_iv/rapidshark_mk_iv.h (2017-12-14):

/*
 * rapidshark_mk_iv.h
 *
 * Arduino microcontroller code to do All The Things to make darts fly. Various
 * defines, consts, enums and other programming wankery.
 *
 * Author: Sean "schizobovine" Caulfield <sean@yak.net>
 * License: GPLv2 (firmware) / CC4.0-BY-SA (documentation, hardware)
 *
 */

#ifndef __RAPIDSHARK_MK_IV_h
#define __RAPIDSHARK_MK_IV_h

////////////////////////////////////////////////////////////////////////
// CONSTANTS
////////////////////////////////////////////////////////////////////////

//
// Pin assignments
//


#define PIN_SW_PUSH     2
#define PIN_ACCEL_PWM   3
#define PIN_SW_CLIP     4
#define PIN_SW_ACCEL    5
#define PIN_SW_FIRE     6
#define PIN_PUSH_A      7
#define PIN_TACHOMETER  8
#define PIN_PUSH_B      9
#define PIN_PUSH_PWM    11
#define PIN_BUTT        13
#define PIN_DISP_RST    -1

//
// Display parameters
//

#define DISP_TEXT_SMALL 1
#define DISP_TEXT_LARGE 2
#define DISP_COLOR      WHITE
#define DISP_ADDR       0x3C
#define DISP_MODE       SSD1306_SWITCHCAPVCC

//
// Motor speed settings
//

#define MOTOR_ACCEL_SPEED     128
#define MOTOR_ACCEL_SPEED_MAX 255
#define MOTOR_PUSH_SPEED      96

// Number of microseconds per rotational period for 20krpm, the measured
// average speed at half-throttle, so we can full-throttle accelerate to that
// speed.
//
//                1
// tau = -------------------- * 1000 (ms/sec) * 1000 (us/ms)
//       20krpm / 60(sec/min)
//     = 60 * 1000 * 1000 / 20000 us
//     = 3000 us

#define MOTOR_ACCEL_SET_PERIOD (3000)

//
// Debounce intervals (in ms)
//

#define DEBOUNCE_TACHOMETER   (1)
#define DEBOUNCE_PUSH         (1)
#define DEBOUNCE_CLIP         (10)
#define DEBOUNCE_FIRE         (10)
#define DEBOUNCE_ACCEL        (10)
#define DEBOUNCE_BUTT         (10)

//
// Helper macros for readability
//
#define IS_PUSHER_EXTENDED  (switchPusher.read()==HIGH)
#define IS_PUSHER_RETRACTED (switchPusher.read()==LOW)
#define IS_ACC_TRIG_OPEN    (switchAccelTrigger.read()==HIGH)
#define IS_ACC_TRIG_CLOSED  (switchAccelTrigger.read()==LOW)
#define IS_FIRE_TRIG_OPEN   (switchFireTrigger.read()==HIGH)
#define IS_FIRE_TRIG_CLOSED (switchFireTrigger.read()==LOW)
#define IS_CLIP_INSERTED    (switchClipDetect.read()==HIGH)

////////////////////////////////////////////////////////////////////////
// PROTOTYPES
////////////////////////////////////////////////////////////////////////

bool finishedAccel();
void setMotorState();

void irq_tach_sens();
void irq_sw_push();
void irq_sw_clip();
void irq_sw_fire();
void irq_sw_accel();
void irq_butt_x();
void irq_butt_y();
void irq_butt_z();

void displayDecimal(uint8_t x, uint8_t y, int num);
void displayLabel(uint8_t x, uint8_t y, const char *text, bool invert);
void displayTextNormal();
void displayTextFlipped();
void displayRefresh();
void displayInit();
void displayDebugData();

void setup();
void loop();

#endif

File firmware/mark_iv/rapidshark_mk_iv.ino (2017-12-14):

/*
 * rapidshark_mk_iv.ino
 *
 * Arduino microcontroller code to do All The Things to make darts fly.
 *
 * Author: Sean "schizobovine" Caulfield <sean@yak.net>
 * License: GPLv2 (firmware) / CC4.0-BY-SA (documentation, hardware)
 *
 */

#include <stdlib.h>
#include <stdio.h>
#include <string.h>
#include <math.h>
#include <limits.h>
#include <avr/io.h>
#include <avr/pgmspace.h>
#include <avr/power.h>
#include <avr/sleep.h>

#include <Arduino.h>
#include <SPI.h>
#include <Wire.h>
#include <Adafruit_GFX.h>
#include <Adafruit_SSD1306.h>
#include <EnableInterrupt.h>
#include <Bounce2.h>

#include "vnh5019.h"
#include "firemode.h"
#include "clip.h"
#include "tach.h"
#include "rapidshark_mk_iv.h"

#define SERIAL_DEBUG 1
#define SERIAL_BAUD_RATE 9600

#if SERIAL_DEBUG
#define DEBUG_PRINTLN(msg) Serial.println((msg))
#define DEBUG_PRINT(msg) Serial.print((msg))
#else
#define DEBUG_PRINTLN(msg)
#define DEBUG_PRINT(msg)
#endif

////////////////////////////////////////////////////////////////////////
// GLOBAL STATE VARIABLES
////////////////////////////////////////////////////////////////////////

// Display controller
Adafruit_SSD1306 display(PIN_DISP_RST);

// Monitor flywheel rotational velocity
Tachometer tach;

// Motor controllers
VNH5019 motor_push  = VNH5019(PIN_PUSH_A,  PIN_PUSH_B,  PIN_PUSH_PWM,  MOTOR_PUSH_SPEED);

// Button/switch debouncers
Bounce tachSensor;
Bounce switchPusher;
Bounce switchClipDetect;
Bounce switchFireTrigger;
Bounce switchAccelTrigger;
Bounce butt;

// Current & total ammo counters
AmmoClip ammo_clip(CLIP_DEFAULT);

// Current fire control mode
FireMode fireMode(MODE_FULL_AUTO);

// Maximum RPM for display
volatile float _max_rpm = 0.0;
volatile uint8_t accel_speed = 0;

////////////////////////////////////////////////////////////////////////
// MOTOR STATE MACHINE
////////////////////////////////////////////////////////////////////////

/*
 * finishedAccel()
 *
 * Returns true if the flywheels are rotating at their set point speed or
 * higher. Used to throttle flywheel motors to maximize acceleration while not
 * destroying them.
 *
 */
bool finishedAccel() {
  //uint16_t tau = tach.tau();
  //if (tau != 0 && tau <= MOTOR_ACCEL_SET_PERIOD) {
  //  return true;
  //}
  return false;
}

/*
 * setMotorState() 
 *
 * Called to figure out if motors should freewheel, brake or go, all based on
 * current system state (is the pusher switch open, fire/accel triggers, and
 * finally fire control mode all factor in). In the stock Rapid Strike, this is
 * handled via eletromechanics such that the three switches comprise the entire
 * state machine. We have to simulate that here.
 *
 */
void setMotorState() {
  
  /*********************************************************************
   *                               PUSHER                              *
   *********************************************************************/

  // If pusher switch is open, this means it's extended outward and needs to be
  // retracted no matter what;
  if (IS_PUSHER_EXTENDED) {
    motor_push.go();

  // If the fire trigger is open, user has let go of it, and so yank brake to
  // stop pusher and thus stop firing.
  } else if (IS_FIRE_TRIG_OPEN) {
    motor_push.brake();

  // Trigger held down, so activate depending on fire control mode and
  // potentially burst counter: keep plugging away for full auto mode; for
  // burst/semi, only activate if we have shots remaining
  } else if (fireMode.keepFiringAssholes()) {
      motor_push.go();

  // Otherwise brake motor
  } else {
    motor_push.brake();
  }
  
  /*********************************************************************
   *                            FLYWHEELS                              *
   *********************************************************************/

  // If the acceleration trigger is being pushed OR if the fire trigger is
  // being pushed & we're supposed to be firing, run motors
  if (IS_ACC_TRIG_CLOSED || (IS_FIRE_TRIG_CLOSED && fireMode.keepFiringAssholes())) {

    // If we're not at speed, floor it
    if (finishedAccel()) {
      analogWrite(PIN_ACCEL_PWM, MOTOR_ACCEL_SPEED_MAX);
      accel_speed = MOTOR_ACCEL_SPEED_MAX;

    // Already looks like we're at speed, so just use normal throttle setting
    } else {
      analogWrite(PIN_ACCEL_PWM, MOTOR_ACCEL_SPEED);
      accel_speed = MOTOR_ACCEL_SPEED;
    }

  // Otherwise, brake motor (and reset tach)
  } else {
    analogWrite(PIN_ACCEL_PWM, 0);
    accel_speed = 0;
    _max_rpm = tach.getMaxRPM();
    tach.reset();
  }

}

////////////////////////////////////////////////////////////////////////
// INTERRUPT HANDLERS
////////////////////////////////////////////////////////////////////////

/*
 * irq_tach_sens - Called when IR sensor "sees" the IR LED behind the flywheel,
 * i.e., one rotation has completed.
 */
void irq_tach_sens() {
  if (tachSensor.update() && tachSensor.fell()) {
    tach.mark();
  }
}

/*
 * irq_sw_push - Called when the pusher switch opens/closes
 */
void irq_sw_push() {

  // Read switch value and if and only if it's changed, change some state
  if (switchPusher.update()) {

    // If the pusher limit switch is closing, the arm is almost full retracted,
    // meaning we've just completed a single fire cycle. In limited fire modes,
    // this means we should mark off one shot taken.
    if (switchPusher.fell()) {
      fireMode.decBurstCount();
      ammo_clip.decrement();
    }

    // Change motor states if needed
    setMotorState();

  }
}

/*
 * irq_sw_clip - Called when the clip insert detection switch changed
 */
void irq_sw_clip() {
  if (switchClipDetect.update() && switchClipDetect.fell()) {
    ammo_clip.reset();
  }
}

/*
 * irq_sw_fire - Called when the fire trigger is pulled/released
 */
void irq_sw_fire() {

  // Read switch value and if and only if it's changed, change some state
  if (switchFireTrigger.update()) {

    // On falling signal (user is just starting to close the switch, so pulling
    // the trigger to fire), set the burst counter if we're in that mode.
    if (switchFireTrigger.fell()) {
      fireMode.resetBurstCount();

    // On the rising signal (user is letting go of the trigger and it's just
    // opening again), reset burst counter to zero.
    } else if (switchFireTrigger.rose()) {
      fireMode.zeroBurstCount();
    }

    // Change motor states if needed
    setMotorState();
  }
}

/*
 * irq_sw_accel - Called when the acceleration trigger is pulled/released
 */
void irq_sw_accel() {
  if (switchAccelTrigger.update()) {
    setMotorState();
  }
}

/*
 * irq_butt - Called when user presses the button (down only)
 */
void irq_butt() {
  if (butt.update() && butt.fell()) {
    fireMode.nextMode();
  }
}

////////////////////////////////////////////////////////////////////////
// STARTUP CODE
////////////////////////////////////////////////////////////////////////
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

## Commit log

2015-09-09 checkin of hardware files so far and firmware
    [rapidshark-battery-conn-mk-1.0.brd, rapidshark-battery-conn-mk-1.0.sch, rapidshark-battery-conn-mk-1.1.brd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]
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2015-10-02 various new versions of the main connector board
    [rapidshark-main-breakout-top-mk-1.7-fab.brd, rapidshark-main-breakout-top-mk-1.7-fab.sch, rapidshark-main-breakout-top-mk-1.7.brd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]
2015-10-02 level shifter for the *@(^+ SparkFun OLED
    [rapidshark-display-shifter-mk-1.0.brd, rapidshark-display-shifter-mk-1.0.sch]
2015-10-03 smaller connector board to squeeze past the big ass cap
    [rapidshark-motor-connector-mk-1.2.brd, rapidshark-motor-connector-mk-1.2.sch]
2015-10-03 you know, i don't think i have enough revisions of this yet
    [rapidshark-main-breakout-top-mk-1.10.brd, rapidshark-main-breakout-top-mk-1.10.sch, rapidshark-main-breakout-top-mk-1.9.brd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]
2015-10-16 tweaks to jst part hole sizes
    [rapidshark-main-breakout-top-mk-1.7-fab.sch, rapidshark-main-breakout-top-mk-1.9.brd, rapidshark-main-breakout-top-mk-1.9.sch]
2015-10-16 various attempts to make a voltmeter to measure cell voltage in the battery
    [rapidshark-lipo-sensor-mk-1.0.brd, rapidshark-lipo-sensor-mk-1.0.sch, rapidshark-lipo-sensor-mk-2.0.brd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]
2015-10-16 attempting to make the sparkfun oled display 5V compatible and easier for i2c
    [rapidshark-display-shifter-mk-1.1.brd, rapidshark-display-shifter-mk-1.1.sch, rapidshark-display-shifter-mk-2.0.brd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]
2015-10-16 first attempt at documenting another oled board for purposes of getting laser cut parts for it
    [oled.brd]
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2015-10-16 actually bothered to layout this one
    [rapidshark-motor-connector-mk-1.1.sch]
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2015-10-18 layout for laser cutting
    [oled-mk-1.1-abs-black-1.5mm.brd, oled-mk-1.1-layer-1.brd, oled-mk-1.1-layer-2.brd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]
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2015-10-18 whoops forgot to remove calibration sq from this one
    [oled-mk-1.1-layer-5.brd]
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2015-10-18 changing to match the ABS one
    [oled-mk-1.1-pmma-clear-0.75mm.brd]
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2015-10-18 exported AutoCAD DXF files
    [oled-mk-1.1-abs-black-1.5mm.dxf, oled-mk-1.1-pmma-clear-0.75mm.dxf]
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2015-10-22 relayout and now provides both 3V and 5V to display (but assumes IO voltage is whatever the arduino sends out
    [rapidshark-main-breakout-top-mk-1.9.brd, rapidshark-main-breakout-top-mk-1.9.sch]
2015-10-22 attempt to build a display butt for sparkfun oled
    [rapidshark-display-shifter-mk-3.0.brd, rapidshark-display-shifter-mk-3.0.sch]
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2015-10-24 renaming nets so i can copypasta into the sketch
    [rapidshark-main-breakout-top-mk-1.7-fab.brd, rapidshark-main-breakout-top-mk-1.7-fab.sch]
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2015-10-28 removing this board that's not gonna get made
    [rapidshark-main-breakout-top-mk-1.10.brd, rapidshark-main-breakout-top-mk-1.10.sch]
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2015-10-28 renaming -fab files to their parents since that was dumb
    [rapidshark-main-breakout-top-mk-1.4.brd, rapidshark-main-breakout-top-mk-1.4.sch, rapidshark-main-breakout-top-mk-1.5.brd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]
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2015-10-28 use QSE-159 optoswitch for better noise immunity
    [rapidshark-dart-detector-mk-2.1.brd, rapidshark-dart-detector-mk-2.1.sch]
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2015-10-28 simplified resistor add without reset or 3.3V to display
    [rapidshark-main-breakout-top-mk-1.B.brd, rapidshark-main-breakout-top-mk-1.B.sch]
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2015-11-07 new version to tweak a few layout/silkscreen issues
    [rapidshark-display-shifter-mk-3.1.brd, rapidshark-display-shifter-mk-3.1.sch]
2015-11-08 fixed silkscreen on 0602 resistor package
    [rapidshark-display-shifter-mk-3.1.brd, rapidshark-display-shifter-mk-3.1.sch]
2015-11-10 rework to include sleeping, separate header file, motor object changes
    [rapidshark_mk_iv.h, rapidshark_mk_iv.ino, vnh5019.cpp]
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2015-11-22 Revert "breaking out fire mode control"
    This reverts commit fe47e61f974774da0fce26976c971ae77f6df7a7.
    [rapidshark_mk_iv.h, rapidshark_mk_iv.ino]
2015-11-22 Revert "Revert "breaking out fire mode control""
    This reverts commit 9375ccac8e7b97cbc899d3c130f71f3d9cef65df.
    [rapidshark_mk_iv.h, rapidshark_mk_iv.ino]
2015-11-22 Restoring multi-button code but keeping sleeping
    This reverts commit eb53e6b5dc9cd32bc981d69df92df141fb3282ce.
    Conflicts:
    firmware/mark_iv/rapidshark_mk_iv.ino
    [rapidshark_mk_iv.h, rapidshark_mk_iv.ino]
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2015-11-22 i hate c++, but ammo counter now broken out
    [rapidshark_mk_iv.ino]
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2015-11-22 works! fixed bug where pusher wasn't fully retracting due to pwm cycle not being high enough to fully brake motor
    [rapidshark_mk_iv.h, rapidshark_mk_iv.ino, vnh5019.cpp]
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2015-11-29 herp derp inverted period and freq; disabling tach results until buffer full
    [rapidshark_mk_iv.ino]
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2015-12-08 attempts at my own very special and not good h bridge
    [rapidshark-h-bridge-mk-1.0.brd, rapidshark-h-bridge-mk-1.0.sch, rapidshark-h-bridge-mk-2.0.brd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]
2015-12-08 some more compilation fixes
    [battery_tester.ino]
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2016-02-02 unfinished hardware design for a battery level tester which reports over SPI/I2c
    [rapidshark-lipo-sensor-mk-2.2.brd, rapidshark-lipo-sensor-mk-2.2.sch]
2016-02-02 unfinished new revision of OLED backpack for sparkfun's microview breakout after a single attempt at building one
    [rapidshark-display-shifter-mk-3.2.brd, rapidshark-display-shifter-mk-3.2.sch]
2016-02-02 a number of smaller discrete mosfet partial bridges to hit accceleration target
    [rapidshark-half-assed-half-h-bridge-mk-1.0.brd, rapidshark-half-assed-half-h-bridge-mk-1.0.sch, rapidshark-nmos-quarter-bridge-mk-1.0.brd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]
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2016-04-16 adding these to commit to log before shifting to another repo
    [rapidshark-display-shifter-mk-4.0.sch, rapidshark-display-shifter-mk-4.1.brd, rapidshark-display-shifter-mk-4.1.sch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]
2016-04-16 removing now in uvdosimeter repo where they belong
    [rapidshark-display-shifter-mk-4.0.brd, rapidshark-display-shifter-mk-4.0.sch, rapidshark-display-shifter-mk-4.1.brd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]
2016-08-17 motor butt plate to make less EM farts
    [rapidshark-motor-filter-mk-1.0.brd, rapidshark-motor-filter-mk-1.0.sch]
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2016-09-07 yet more twiddling around with cheap h-bridge ideas
    [rapidshark-half-assed-half-h-bridge-mk-1.2.brd, rapidshark-half-assed-half-h-bridge-mk-1.2.sch, rapidshark-half-assed-half-h-bridge-mk-1.3.brd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]
2016-09-07 first pass BLDC ESC, this should end well
    [rapidshark-half-assed-bldc-esc-mk-1.0.brd, rapidshark-half-assed-bldc-esc-mk-1.0.sch]
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2016-10-02 fix revision on silkscreen/board
    [rapidshark-main-breakout-top-mk-1.B.brd]
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2016-10-29 look i change my mind a lot ok
    [rapidshark-forward-breakout-mk-1.1.brd, rapidshark-forward-breakout-mk-1.1.sch]
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2017-02-14 new connector board for new motor driver and lipo sensor
    [rapidshark-main-breakout-top-mk-1.C.brd, rapidshark-main-breakout-top-mk-1.C.sch]
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2017-10-05 oh hey more hardware fails
    [rapidshark-forward-breakout-mk-1.2.brd, rapidshark-forward-breakout-mk-1.2.sch, rapidshark-lipo-sensor-mk-3.7.brd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]
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

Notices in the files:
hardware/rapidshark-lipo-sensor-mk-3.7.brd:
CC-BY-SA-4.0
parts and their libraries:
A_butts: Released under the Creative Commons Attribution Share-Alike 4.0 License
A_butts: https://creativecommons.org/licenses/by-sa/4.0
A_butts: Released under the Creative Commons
